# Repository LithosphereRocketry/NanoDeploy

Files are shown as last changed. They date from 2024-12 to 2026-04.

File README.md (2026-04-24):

# NanoDeploy

## Firmware

Firmware for NanoDeploy is located in the `firmware` directory. Most day-to-day
operations are handled by that folder's Makefile.

### Build environment setup

The setup process for TI's MSP430 toolchain is pretty miserable on modern Linux.
See firmware/install-notes.md for details.

### Uploading

Run `make run` to upload the code to an attached MSP430 development board.

### Debugging

Run `make gdb` to upload the code to the attached dev board and start a GDB
server session. From a separate terminal, then run `msp430-gdb`. (The included
.gdbinit file should take care of all the necessary setup.)

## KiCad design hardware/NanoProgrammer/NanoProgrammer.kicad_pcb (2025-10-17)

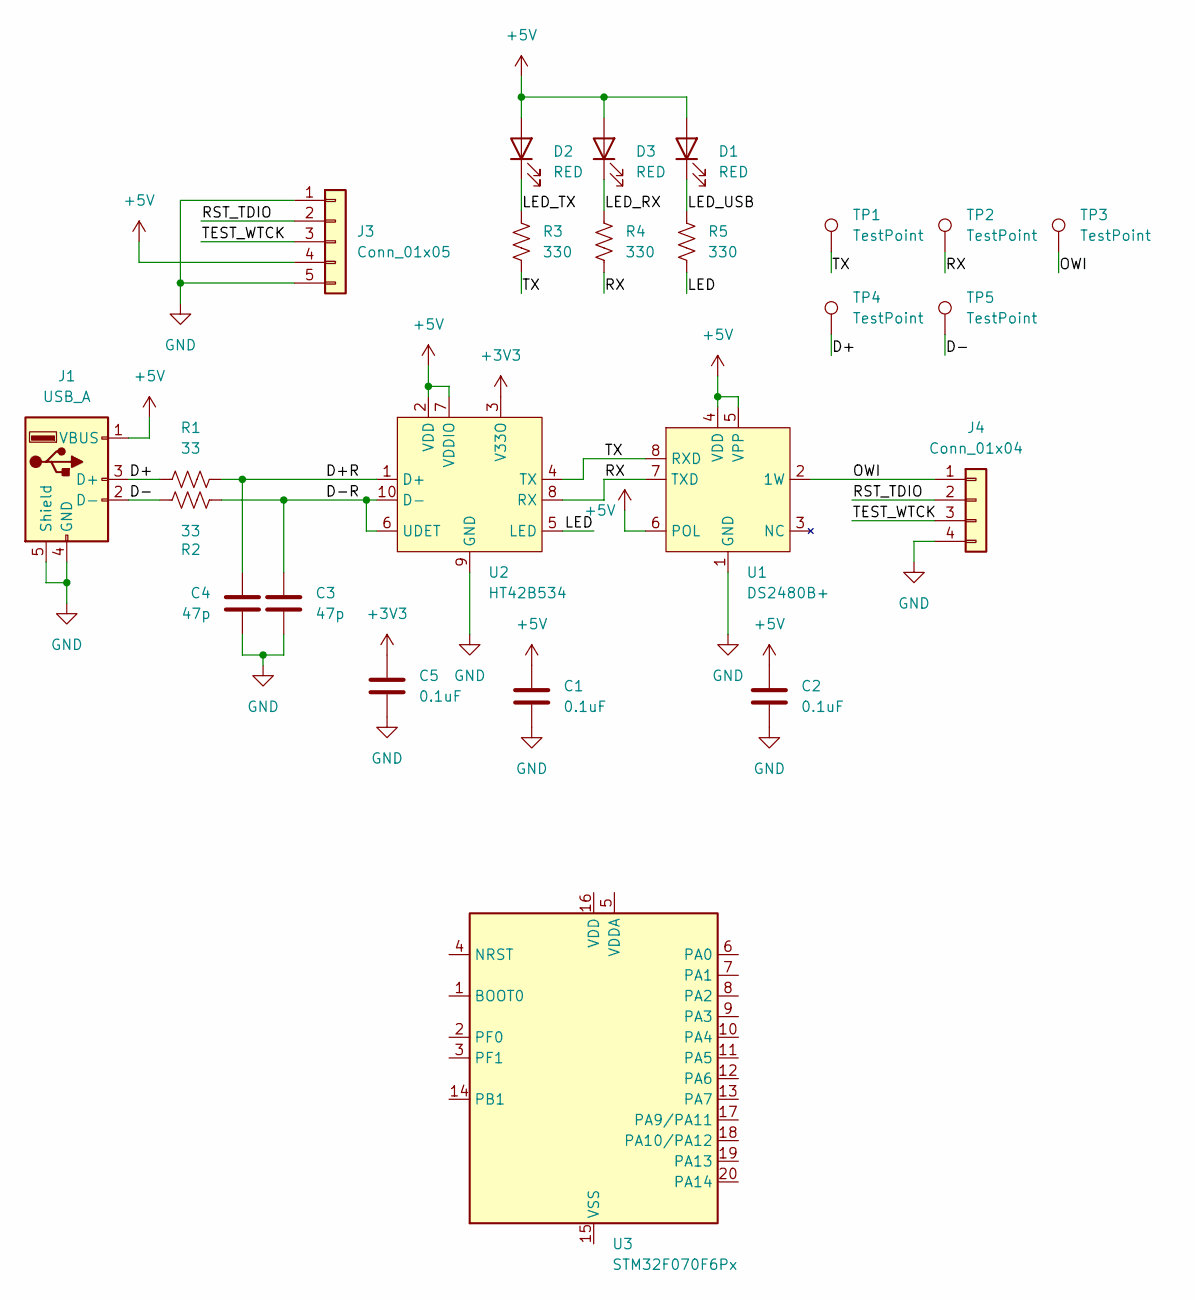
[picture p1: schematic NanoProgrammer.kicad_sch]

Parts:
C1, C2, C5: 0.1uF; C_0402_1005Metric; LCSC C1525
C3, C4: 47p; C_0402_1005Metric; LCSC C1567
D1, D2, D3: RED; LED_0603_1608Metric; LCSC C2286
J1: USB_A; USB_A_AdamTech_USB-AP-S-RA_Horizontal; JLCPCB_IGNORE ignore
J3: Conn_01x05; PinHeader_1x05_P2.54mm_Vertical; JLCPCB_IGNORE ignore
J4: Conn_01x04; Molex_PicoBlade_53047-0410_1x04_P1.25mm_Vertical; JLCPCB_IGNORE ignore
R1, R2: 33; R_0402_1005Metric; LCSC C25105
R3, R4, R5: 330; R_0402_1005Metric; LCSC C25104
TP1, TP2, TP3, TP4, TP5: TestPoint; TestPoint_THTPad_1.0x1.0mm_Drill0.5mm; JLCPCB_IGNORE ignore
U1: DS2480B+; SO-8_3.9x4.9mm_P1.27mm; LCSC C722462
U2: HT42B534; SSOP-10_3.9x4.9mm_P1.00mm; LCSC C493293
U3: STM32F070F6Px; TSSOP-20_4.4x6.5mm_P0.65mm

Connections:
+3V3: C5.1, U2.3 (V33O)
+5V: C1.1, C2.1, D1.2 (A), D2.2 (A), D3.2 (A), J1.1 (VBUS), J3.4, U1.4 (VDD), U1.5 (VPP), U1.6 (POL), U2.2 (VDD), U2.7 (VDDIO)
/D+: J1.3 (D+), R1.1, TP4.1
/D+R: C4.1, R1.2, U2.1 (D+)
/D-: J1.2 (D-), R2.1, TP5.1
/D-R: C3.1, R2.2, U2.6 (UDET), U2.10 (D-)
/LED: R5.1, U2.5 (LED)
/LED_RX: D3.1 (K), R4.2
/LED_TX: D2.1 (K), R3.2
/LED_USB: D1.1 (K), R5.2
/OWI: J4.1, TP3.1, U1.2 (1W)
/RST_TDIO: J3.2, J4.2
/RX: R4.1, TP2.1, U1.7 (TXD), U2.8 (RX)
/TEST_WTCK: J3.3, J4.3
/TX: R3.1, TP1.1, U1.8 (RXD), U2.4 (TX)
GND: C1.2, C2.2, C3.2, C4.2, C5.2, J1.4 (GND), J1.5 (Shield), J3.1, J3.5, J4.4, U1.1 (GND), U2.9 (GND)

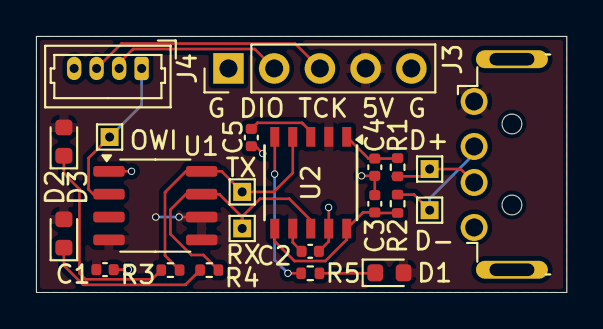
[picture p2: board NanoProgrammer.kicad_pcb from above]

Board: 2 copper layers, 29.5 x 14.2 mm, 23 parts (0 on the bottom side), 16 nets.

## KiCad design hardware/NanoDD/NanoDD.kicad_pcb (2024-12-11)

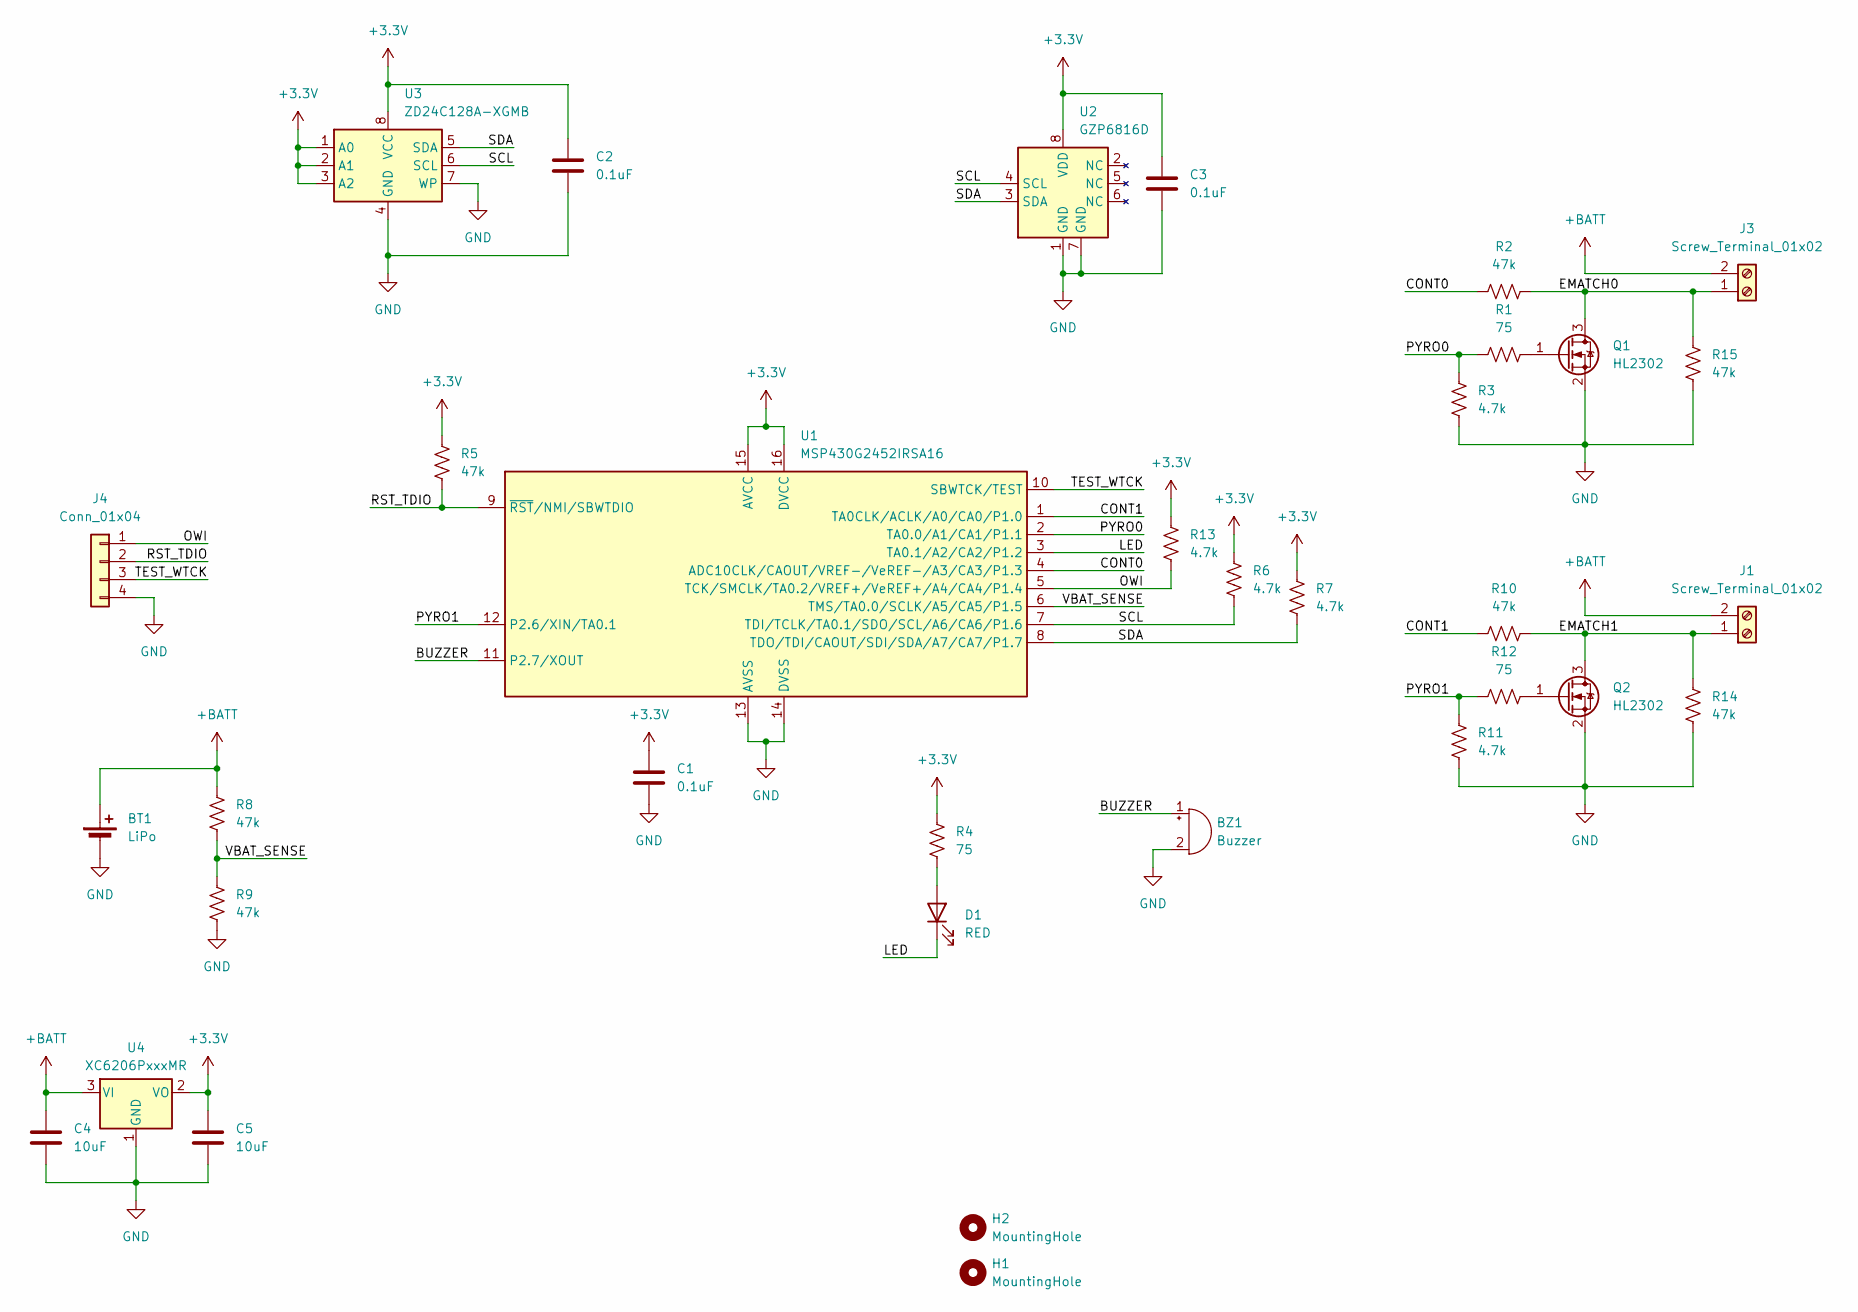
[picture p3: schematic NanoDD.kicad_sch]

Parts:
BT1: LiPo; PinHeader_1x02_P2.00mm_Vertical; JLCPCB_IGNORE ignore
BZ1: Buzzer; Buzzer_CUI_CPT-9019S-SMT; JLCPCB_IGNORE ignore
C1, C2, C3: 0.1uF; C_0402_1005Metric; LCSC C1525
C4, C5: 10uF; C_0603_1608Metric; LCSC C19702
D1: RED; LED_0603_1608Metric; LCSC C2286
H1, H2: MountingHole; MountingHole_2.2mm_M2; JLCPCB_IGNORE ignore
J1, J3: Screw_Terminal_01x02; TerminalBlock_TE_282834-2_1x02_P2.54mm_Horizontal; JLCPCB_IGNORE ignore
J4: Conn_01x04; Molex_PicoBlade_53047-0410_1x04_P1.25mm_Vertical; JLCPCB_IGNORE ignore
Q1, Q2: HL2302; SOT-23; LCSC C28646268
R1, R4, R12: 75; R_0402_1005Metric; LCSC C25133
R2, R5, R8, R9, R10, R14, R15: 47k; R_0402_1005Metric; LCSC C25792
R3, R6, R7, R11, R13: 4.7k; R_0402_1005Metric; LCSC C2906941
U1: MSP430G2452IRSA16; Texas_RSA_VQFN-16-1EP_4x4mm_P0.65mm_EP2.7x2.7mm; LCSC C74965
U2: GZP6816D; Bosch_LGA-8_2x2.5mm_P0.65mm_ClockwisePinNumbering; LCSC C3038127
U3: ZD24C128A-XGMB; TSSOP-8_4.4x3mm_P0.65mm; LCSC C918272
U4: XC6206PxxxMR; SOT-23-3; LCSC C5446

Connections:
+3.3V: C1.1, C2.1, C3.1, C5.1, R4.2, R5.1, R6.1, R7.1, R13.1, U1.15 (AVCC), U1.16 (DVCC), U2.8 (VDD), U3.1 (A0), U3.2 (A1), U3.3 (A2), U3.8 (VCC), U4.2 (VO)
+BATT: BT1.1 (+), C4.1, J1.2, J3.2, R8.1, U4.3 (VI)
/BUZZER: BZ1.1 (+), U1.11 (P2.7/XOUT)
/CONT0: R2.1, U1.4 (ADC10CLK/CAOUT/VREF-/VeREF-/A3/CA3/P1.3)
/CONT1: R10.1, U1.1 (TA0CLK/ACLK/A0/CA0/P1.0)
/EMATCH0: J3.1, Q1.3 (D), R2.2, R15.2
/EMATCH1: J1.1, Q2.3 (D), R10.2, R14.2
/LED: D1.1 (K), U1.3 (TA0.1/A2/CA2/P1.2)
/OWI: J4.1, R13.2, U1.5 (TCK/SMCLK/TA0.2/VREF+/VeREF+/A4/CA4/P1.4)
/PYRO0: R1.2, R3.1, U1.2 (TA0.0/A1/CA1/P1.1)
/PYRO1: R11.1, R12.2, U1.12 (P2.6/XIN/TA0.1)
/RST_TDIO: J4.2, R5.2, U1.9 (~RST/NMI/SBWTDIO)
/SCL: R6.2, U1.7 (TDI/TCLK/TA0.1/SDO/SCL/A6/CA6/P1.6), U2.4 (SCL), U3.6 (SCL)
/SDA: R7.2, U1.8 (TDO/TDI/CAOUT/SDI/SDA/A7/CA7/P1.7), U2.3 (SDA), U3.5 (SDA)
/TEST_WTCK: J4.3, U1.10 (SBWTCK/TEST)
/VBAT_SENSE: R8.2, R9.1, U1.6 (TMS/TA0.0/SCLK/A5/CA5/P1.5)
GND: BT1.2 (-), BZ1.2 (-), C1.2, C2.2, C3.2, C4.2, C5.2, J4.4, Q1.2 (S), Q2.2 (S), R3.2, R9.2, R11.2, R14.1, R15.1, U1.13 (AVSS), U1.14 (DVSS), U2.1 (GND), U2.7 (GND), U3.4 (GND), U3.7 (WP), U4.1 (GND)
unnamed: D1.2 (A), R4.1
unnamed: Q1.1 (G), R1.1
unnamed: Q2.1 (G), R12.1

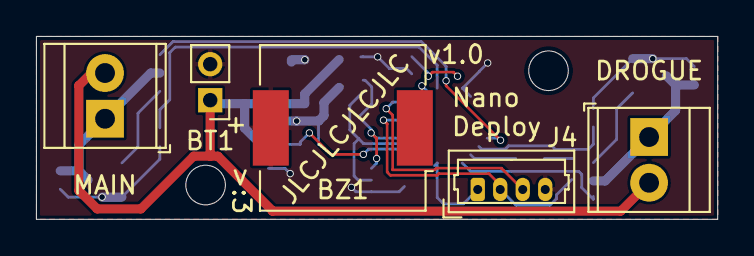
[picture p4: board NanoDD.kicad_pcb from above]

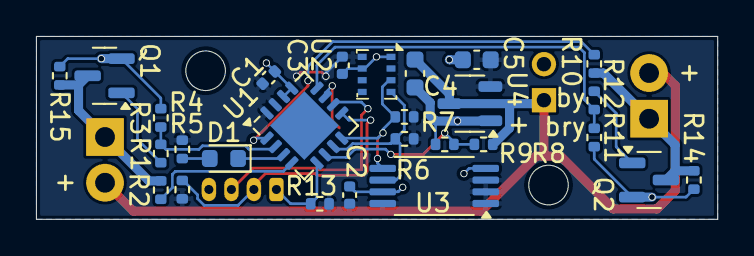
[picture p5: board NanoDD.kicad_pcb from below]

Board: 2 copper layers, 37.8 x 10.2 mm, 34 parts (27 on the bottom side), 20 nets.

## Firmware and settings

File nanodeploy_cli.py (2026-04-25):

#!/usr/bin/python3
import typing
import serial
import serial.serialutil
import argparse
import tqdm

import nano_owi_bridge as owi
from nanodeploy import *

def getval(msg: str, func: typing.Callable, default: typing.Any = None, onfail: None | str = None) -> typing.Any:
    if onfail is None:
        onfail = f"Input must be of type {func.__name__}"
    if default is not None:
        msg += f" ({default})"
    while True:
        try:
            instr = input(msg)
            if instr == "" and default is not None:
                return default
            return func(instr)
        except ValueError:
            print(onfail)

def cmd_help(*_: list[str]):
    print("NanoDeploy CLI interface commands:")
    for name, (help, _) in commands.items():
        print(f"{name}\t{help}")

def cmd_quit(*_: list[str]):
    exit(0)

def cmd_list(*_: list[str]):
    ensure_cfg()
    print(config)

def cmd_port(*args: str):
    global port
    if len(args) < 1:
        print("Not enough arguments to port command")
        return
    try:
        port = serial.Serial(args[0], 115200)
        print(f"Using port {args[0]}")
    except serial.SerialException:
        print(f"Couldn't open port {args[0]}")
            
def write_default(dev_id: DeviceID, name: str):
    default_config = Config(dev_id, name)
    write_config(port, bytes(default_config))

def prompt_id(prev: typing.Optional[DeviceID] = None) -> DeviceID:
    if prev is not None:
        hwver = getval("Hardware revision?", int, prev.hwver)
        fwver = getval("Firmware revision?", int, prev.hwver)
        id = getval("ID number?", int, prev.id)
    else:
        hwver = getval("Hardware revision?", int)
        fwver = getval("Firmware revision?", int)
        id = getval("ID number?", int)
    return DeviceID(hwver, fwver, id)

def cmd_dump(*args: str):
    if len(args) < 1:
        print("Not enough arguments to dump command")
        return
    cmd_read()
    if port is None:
        return
    print("Downloading flight data...")
    with open(args[0], "w") as f:
        f.write(read_data(port, tqdm.tqdm))
    print(f"Wrote data to {args[0]}")

def cmd_read(*_: list[str]):
    global config
    if port is None:
        print("Please select a port first")
        return
    owi.cmd_reset_scan(port)
    owi_id = owi.cmd_scan(port)
    if owi_id is None:
        print("No device found")
        return
    dev_id = DeviceID.from_bytes(owi_id)
    if dev_id is None:
        print(f"Device {owi_id} is corrupted or not a NanoDeploy")
        print("Attempt to reflash with default config?")
        inp = input("(Y/n)").lower()
        if inp not in ["", "y", "yes"]:
            return
        hwver = getval("Hardware revision?", int)
        fwver = getval("Firmware revision?", int)
        id = getval("ID number?", int)
        name = getval("Name?", str)
        write_default(DeviceID(hwver, fwver, id), name)
    new_config = Config.from_bytes(read_config(port))
    if new_config is None:
        if dev_id is not None:
            print(f"Device {owi_id} is a NanoDeploy but its configuration is invalid")
            print("Attempt to reflash with default config?")
            inp = input("(Y/n)").lower()
            if inp not in ["", "y", "yes"]:
                return
            name = getval("Name?", str)
            write_default(dev_id, name)
            new_config = Config.from_bytes(read_config(port))
    if new_config is None:
        print("Failed to write default config!")
        return
    config = new_config
    print("Read configuration data from device")

def cmd_write(*_: list[str]):
    if port is None:
        print("Please select a serial port")
        return
    if config is None:
        print("Please load a configuration first")
        return
    owi.cmd_reset_scan(port)
    owi_id = owi.cmd_scan(port)
    if owi_id is None:
        print("No device found")
        return
    write_config(port, bytes(config))
    print("Saved configuration to device")

def ensure_cfg() -> bool:
    global config
    if config is None and port is not None:
        print("No config loaded, pulling from device")
        cmd_read()
    if config is None:
        print("No config loaded, creating a default config")
        name = getval("Name?", str)
        config = Config(prompt_id(None), name)
        return True
    return False

def cmd_set_id(*_: list[str]):
    if not ensure_cfg():
        config.id = prompt_id(config.id)

def cmd_set_name(*_: list[str]):
    if not ensure_cfg():
        name = getval("Name?", str, config.name)
        config.name = name

def cmd_load(*args: list[str]):
    global port
    ensure_cfg()
    config.load_config(args[0])

def cmd_save(*args: list[str]):
    global port
    if len(args) < 1:
        print("Not enough arguments to save command")
        return
    if config is None:
        print("No config loaded")
    else:
        config.save_config(args[0])

def cmd_default(*_: list[str]):
    global config
    ensure_cfg()
    config = Config(config.id, config.name)
    print("Loaded default parameters")

commands: dict[str, tuple[str, typing.Callable[..., None]]] = {
    "help": ("Prints this help file", cmd_help),
    "quit": ("Exits CLI", cmd_quit),
    "list": ("Prints the currently loaded configuration", cmd_list),
    "port": ("Selects a serial port to search on", cmd_port),
    "dump": ("Downloads flight data to a CSV file", cmd_dump),
    "read": ("Reads configuration data from the device", cmd_read),
    "write": ("Writes configuration data to the device", cmd_write),
    "default": ("Resets the current config to default values", cmd_default),
    "setid": ("Sets a new OneWire id for the device", cmd_set_id),
    "setname": ("Sets a new name for the device", cmd_set_name),
    "load": ("Loads flight parameters from file", cmd_load),
    "save": ("Saves flight parameters to file", cmd_save)
}

port: typing.Optional[serial.Serial] = None
config: typing.Optional[Config] = None

def handle_cmd(inp: str):
    cmd, *args = inp.split()
    if cmd in commands:
        _, func = commands[cmd]
        try:
            func(*args)
        except KeyboardInterrupt:
            print()
    else:
        print(f"Unknown command {cmd}")

def main():
    parser = argparse.ArgumentParser(
        description="Configuration tool for NanoDeploy altimeter."
    )
    parser.add_argument("port", nargs='?', default=None, help="Serial port to search for device on")
    run_group = parser.add_mutually_exclusive_group()
    run_group.add_argument("-r", "--run-command", nargs="+", default=None, help="Run one or more commands rather than running interactively")
    run_group.add_argument("-R", "--run-file", default=None, help="Run one or more commands from a file rather than running interactively")
    args = parser.parse_args()
    if args.port is not None:
        cmd_port(args.port)
    if args.run_command is not None:
        for cmd in args.run_command:
            handle_cmd(cmd)
    elif args.run_file is not None:
        with open(args.run_file) as f:
            for line in f:
                handle_cmd(line)
    else:
        while True:
            try:
                handle_cmd(input("> "))
            except KeyboardInterrupt:
                print()
                cmd_quit()

if __name__ == "__main__":
    main()

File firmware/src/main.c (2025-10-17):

#include <stdint.h>
#include <string.h>
#include <msp430.h>
#include <iomacros.h>

#include "usi_i2c.h"
#include "common.h"
#include "hwconfig.h"
#include "tick.h"
#include "commands.h"
#include "flight_logic.h"
#include "gzp6816d.h"
#include "pins.h"

int main(void) {
    config_clock();
    config_io();

    P1OUT &= ~P_LED;

    __eint();

    i2c_init(USIDIV_4, USISSEL_2); // SMCLK/16 = 1MHz Fast+
    flight_init();

    __dint();
    config_tick();
    __eint();

    while(1) {
        __bis_SR_register(SLEEP_BITS); // Enter LPM0 sleep
        // When we are woken:
        do {
            if(wakeup & WAKE_OWI_CMD) {
                owi_command();
                wakeup &= ~WAKE_OWI_CMD;
            } else if(wakeup & WAKE_OWI_XFER) {
                owi_transfer();
                wakeup &= ~WAKE_OWI_XFER;
            } else if(wakeup & WAKE_TICK) { // Main run loop
                flight_step();
                wakeup &= ~WAKE_TICK;
            }
        } while(wakeup);
    }
}

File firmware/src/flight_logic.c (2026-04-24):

#include "flight_logic.h"

#include <stdlib.h>
#include <string.h>
#include <stdbool.h>

#include "common.h"
#include "pins.h"
#include "gzp6816d.h"
#include "atmosphere.h"
#include "logging.h"
#include "tick.h"
#include "params.h"
#include "adc.h"

#include "generated/kalman_step.h"

#define NUM_CALIB_CYCLES 40

static uint16_t ground_alt;
int16_t kalman_state[] = {0, 0, 0};

static uint8_t log_counter = 0;
static uint8_t state_counter = 0;

static inline uint8_t cont_encode(uint16_t adc) {
    return adc > 0xFE ? 0xFF : adc;
}

static inline void store_log(uint8_t delay, bool tmp) {
    if(log_counter == 0) {
        current_frame->elapsed = elapsed;
        current_frame->altitude = kalman_state[0];
        current_frame->state = flight_state;
        current_frame->batt = adc_buf[5] >> 8;
        current_frame->cont_drogue = cont_encode(adc_buf[3]);
        current_frame->cont_main = cont_encode(adc_buf[0]);
        log_counter = delay;
        if(tmp) log_temp(); else log_store();
    } else {
        log_counter --;
    }
}

void flight_init() {
    adc_init();
    adc_start();
    gzp_request_read(GZP_OSR_PRES_8X, GZP_OSR_TEMP_4X);
}

void flight_step() {
    uint32_t pres_raw, pressure;
    uint16_t temp_raw, alt_meas;
    int16_t kalman_tmp[3];
    gzp_get_raw_data(&pres_raw, &temp_raw);
    gzp_request_read(GZP_OSR_PRES_8X, GZP_OSR_TEMP_4X);

    pressure = gzp_pressure_pa(pres_raw);
    alt_meas = atm_pressure_alt(pressure, /*param->base_pres*/101325UL);
    if(flight_state == STATE_CALIB) {
        static uint32_t base_altitude_acc = 0;
        static size_t calib_cycles = NUM_CALIB_CYCLES;

        base_altitude_acc += alt_meas;
        calib_cycles --;
        if(calib_cycles == 0) {
            ground_alt = base_altitude_acc / NUM_CALIB_CYCLES;
            flight_state = STATE_READY;
            state_counter = param->t_boost;
            P1OUT |= P_LED;
        }
    } else {
        update_kalman(kalman_tmp, kalman_state, alt_meas - ground_alt);
        memcpy(kalman_state, kalman_tmp, sizeof(kalman_state));
        
        state_counter --;
        switch(flight_state) {
            case STATE_READY:
                store_log(param->fd_boost, true);
                if(kalman_state[1] <= param->rate_liftoff*16) {
                    state_counter = param->t_boost;
                } else if(state_counter == 0) {
                    log_flush_temp(current_frame->elapsed);
                    flight_state = STATE_BOOST;
                    state_counter = param->t_coast;
                }
                break;
            case STATE_BOOST:
                store_log(param->fd_boost, false);
                if(kalman_state[1] <= 0 || kalman_state[2] >= 0) {
                    state_counter = param->t_coast;
                } else if(state_counter == 0) {
                    flight_state = STATE_COAST;
                    state_counter = param->t_descent;
                }
                break;
            case STATE_COAST:
                store_log(param->fd_coast, false);
                if(kalman_state[1] >= 0) {
                    state_counter = param->t_coast;
                } else if(state_counter == 0) {
                    // TODO: Fire drogue
                    flight_state = STATE_DESCENT;
                    state_counter = param->t_main;
                }
                break;
            case STATE_DESCENT:
                store_log(param->fd_descent, false);
                if((uint16_t) kalman_state[0] >= param->alt_main) {
                    state_counter = param->t_descent;
                } else if(state_counter == 0) {
                    // TODO: Fire main
                    flight_state = STATE_MAIN;
                    state_counter = param->t_land;
                }
                break;
            case STATE_MAIN:
                store_log(param->fd_main, false);
                if(abs(kalman_state[1]) >= param->rate_land) {
                    state_counter = param->t_main;
                } else if(state_counter == 0) {
                    flight_state = STATE_LANDED;
                }
                break;
            default: break; // should be unreachable
        }
    }
    adc_start();
}

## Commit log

2024-11-16 Initial PCB work
    [NanoDD.kicad_pcb, NanoDD.kicad_sch]
2024-11-16 Oops forgot to sleep and did all the layout
    [NanoDD.kicad_pcb, NanoDD.kicad_sch]
2024-11-18 New PCB with makefile and MS5607
    [NanoDD-CmtUser.gbr, NanoDD-CuBottom.gbl, NanoDD-CuTop.gtl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]
2024-11-18 Deleted excess generated files
    [NanoDD-CmtUser.gbr, NanoDD-CuBottom.gbl, NanoDD-CuTop.gtl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]
2024-11-18 Removed extra copy of pcb
    [NanoDD.kicad_pcb, NanoDD.kicad_sch]
2024-11-20 Even more layout shrink, switch to barometer that's cheap on JLCPCB
    [NanoDD.kicad_pcb, NanoDD.kicad_sch]
2024-11-20 Name and version badge on PCB
    [NanoDD.kicad_pcb]
2024-11-20 Fixed swapped SCL/SDA
    [NanoDD.kicad_pcb, NanoDD.kicad_sch]
2024-11-21 Correct MOSFETs and slightly better routing
    [NanoDD.kicad_pcb, NanoDD.kicad_sch]
2024-12-11 Ported to msp430-gcc because CCS on linux is bad
    [NanoDD.kicad_pcb, NanoDD.kicad_sch]
2024-12-11 Fixed flash test, the issue was that I'm dumb
    [main.c]
2024-12-12 Got timers working
2024-12-12 Switched to TI distribution of GCC, fixed issue with non-static inline, import i2c library
2024-12-24 Programmer board, also a lot of stuff that wasn't committed oops
    [NanoDD.kicad_sch, NanoProgrammer.kicad_pcb, NanoProgrammer.kicad_sch]
2025-01-06 Altitude readings from sensor working
2025-01-08 EEPROM code, minor optimizations to baro code, updated I2C
2025-02-02 Fixed the onewire timeouts, I think
    [main.c]
2025-10-17 huge bunch of uncommitted stuff idk what this is
    [NanoProgrammer.kicad_pcb, NanoProgrammer.kicad_sch, test.csv]
2026-04-24 Work on analog, not done
    [default.cfg, test.csv]
